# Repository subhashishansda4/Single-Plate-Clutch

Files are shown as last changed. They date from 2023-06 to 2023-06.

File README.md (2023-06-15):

## Description
Designed a Single Plate Clutch using mechanical calculations based on the below stated problem and data

**Single Plate Clutch transmitting 7kW power operated with electric motor running at 1400 rpm**

**Raw Data**
* Spline shaft material:-C15Mn75 IS 6967 Steel
* Yield shear strength for IS 6967 Steel =190N/mm2
* Factor of safety for spline shaft=3.0
* Stress concentration factor for spline shaft=2.0
* Rivet material:-Low carbon steel
* Shear stress for rivet material:-42 N/mm2
* No of rivets:-4
* Intensity of pressure for friction lining:- 0.06N/mm2
* Coefficient of friction for friction lining:- 0.15
* Spring Material:- Spring Steel(Stainless Steel)
* Spring Index:-6
* Allowable shear stress for the spring wire:-437.5 N/mm2
* Deflection of spring limited to 6.03 mm
* Modulus of rigidity for spring:-84 x 103 N/mm2
* Angle of pressure plate support:-450
* Bearing type:-Deep groove ball bearing
* Bearing size:-SKF(60 series)
* Bolt material for driving shaft flange:-M.S
* Allowable shear strength for bolt of driving shaft flange=40N/mm2
* Stud & Nut for spring attachment material:-Mild Steel
* Bush material: Brass
* Clutch plate material: Steel
* Pressure plate material: Steel
* Sleeve assembly material: Steel
* Flywheel material: Steel
* Driving shaft material: Steel

### Calculation
The full calculation report can be found here:\
[Calculation Report](https://github.com/subhashishansda4/Single-Plate-Clutch/blob/main/Design%20of%20Single%20Plate%20Clutch.pdf)

## Renders
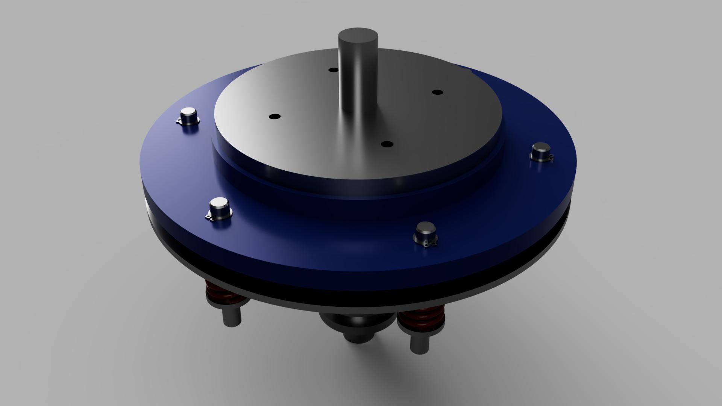
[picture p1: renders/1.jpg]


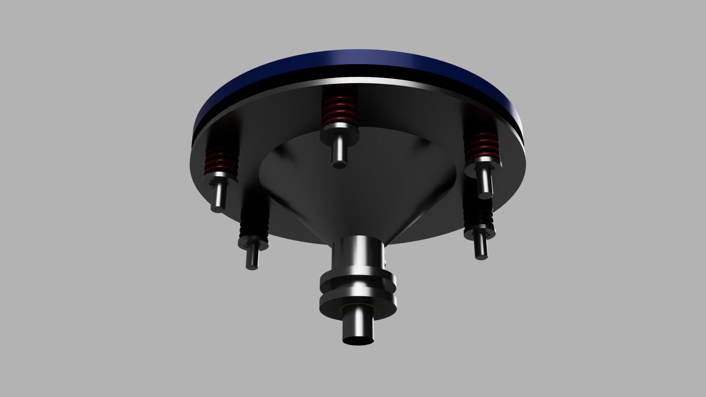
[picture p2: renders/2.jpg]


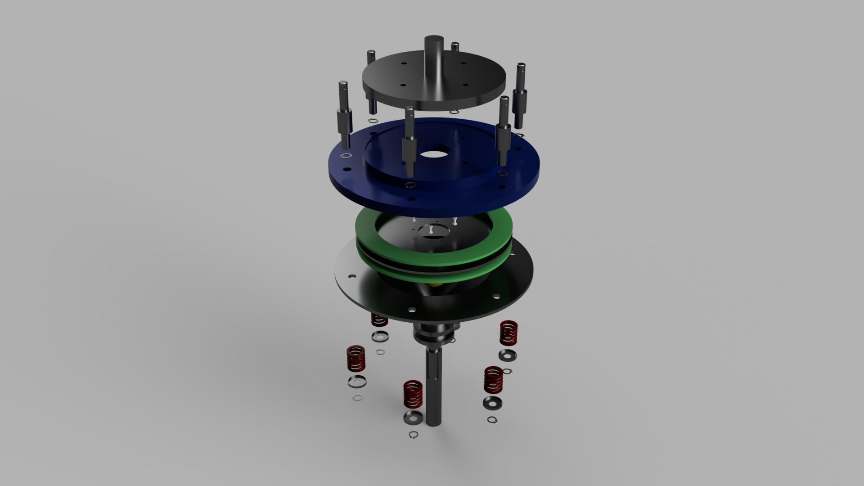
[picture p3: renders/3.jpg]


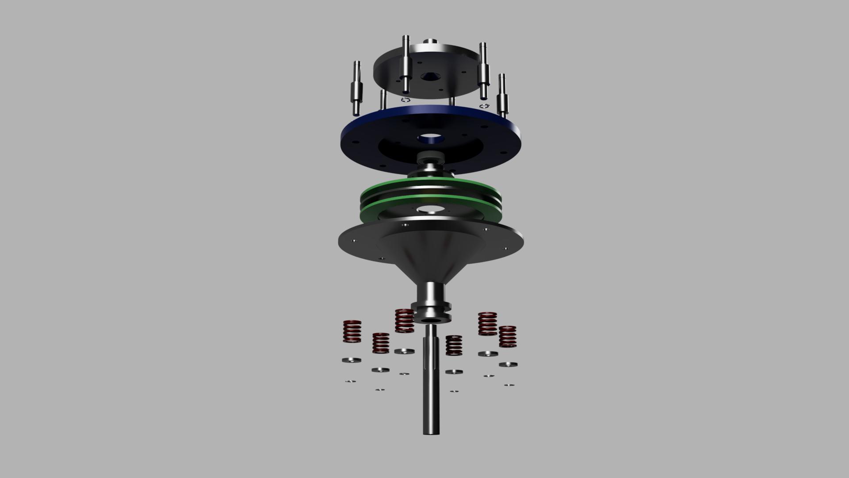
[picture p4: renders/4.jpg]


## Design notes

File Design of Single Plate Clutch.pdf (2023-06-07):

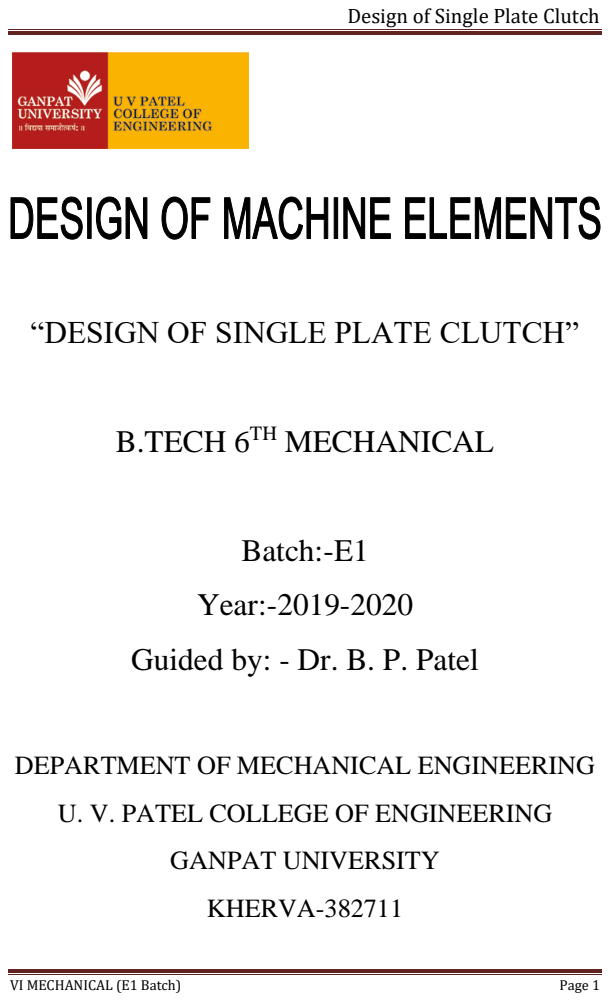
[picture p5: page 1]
VI MECHANICAL (E1 Batch); Page 1; B.TECH 6TH MECHANICAL; GANPAT UNIVERSITY; KHERVA-382711

Design of Single Plate Clutch

“DESIGN OF SINGLE PLATE CLUTCH”

Batch:-E1
Year:-2019-2020
Guided by: - Dr. B. P. Patel

DEPARTMENT OF MECHANICAL ENGINEERING

U. V. PATEL COLLEGE OF ENGINEERING

## CERTIFICATE

### This is to certify that Subhashis Hansda of roll no

17012031044 of 6

### th Mechanical Engineering has

### satisfactorily completed the course work in “Design of Single Plate Clutch” within four walls of U.V. Patel

College of Engineering, Kherva in the year of 2020.

Date of Submission: | Staff In charge

### Head of Department:

### U.V. Patel College of Engineering

### Ganpat University

### Kherva-382711

Design a single plate clutch which transmits 7kW power operated with electric motor running at 1400rpm. Use following data for single plate clutch. Assume the data is required.

- Spline shaft material:-C15Mn75 IS 6967 Steel
- Yield shear strength for IS 6967 Steel =190N/mm²
- Factor of safety for spline shaft=3.0
- Stress concentration factor for spline shaft=2.0
- Rivet material:-Low carbon steel
- Shear stress for rivet material:-42 N/mm²
- No of rivets:-4
- Intensity of pressure for friction lining:- 0.06N/mm²
- Coefficient of friction for friction lining:- 0.15
- Spring Material:- Spring Steel(Stainless Steel)
- Spring Index:-6
- Allowable shear stress for the spring wire:-437.5 N/mm²
- Deflection of spring limited to 6.03 mm
- Modulus of rigidity for spring:-84 x 10³ N/mm²
- Angle of pressure plate support:-45⁰
- Bearing type:-Deep groove ball bearing
- Bearing size:-SKF(60 series)
- Bolt material for driving shaft flange:-M.S
- Allowable shear strength for bolt of driving shaft flange=40N/mm²
- Stud & Nut for spring attachment material:-Mild Steel
- Bush material: Brass
- Clutch plate material: Steel
- Pressure plate material: Steel
- Sleeve assembly material: Steel
- Flywheel material: Steel

- Driving shaft material: Steel

NOTATIONS:-

SPLINE SHAFT

- P=Power to be transmitted=7kW
- N=Speed of the driving& driven shaft=1400rpm
- Ty=Yield shear strength for
- FOS=Factor of safety
- Kts=Stress concentration factor
- n=no of splines
- k=Type of fit
- d=Minor diameter of the spline shaft
- D=Major diameter of the spline shaft
- Ta=Allowable shear strength for spline shaft
- T=Average torque transmitted
- b= width of spline
- h=height of spline
- l=length of spline
- F=Shear force in spline shaft
- Dssb=dia of spline shaft for bearing seating
- Ls=total length of spline shaft

HUB FOR SPLINE SHAFT

- dho=Outer dia of hub , mm
- bh=Width of hub ,mm
- dhf=diameter of hub flange , mm
- LH= length of hub, mm
- Fahf=Axial force for hub flange , N

- thf=thickness of hub flange, mm
- PCDfr=Pitch circle diameter of flange rivet , mm

HUB FLANGE RIVET

- Tfr=Shear stress for hub material , N/mm²
- nr=no of rivets
- Fhfr=shear force for hub flange rivet ,mm
- dfrh=Head diameter of flange rivet, mm
- tfrh=Thickness of head flange rivet, mm
- lr=Standard length of rivet, mm

FRICTION LINING

- rmfl=Mean radius of friction lining
- bfl=Face width of friction lining
- Aff=Area of friction faces
- Wa=Axial force acting on the friction faces
- Pl=Intensity of pressure
- µ=Coefficient of friction
- nfs=no of friction surfaces
- tfl=Thickness of friction liner

CLUTCH PLATE

- r1=Outer radius of clutch plate
- r2=Inner radius of clutch plate
- rmfl=mean radius of clutch plate
- d1=Outer dia of clutch plate
- d2=Inner dia of clutch plate

- tcp=Thickness of clutch plate

SPRING

- Dm=Mean dia. of spring
- dsw=Dia. of spring wire
- Wtas=Total load on spring
- ns=No of springs required for axial load
- Ws=Max. Load on spring
- K=Wahl’s stress factor
- C=spring index
- Ts=Allowable shear stress for the spring wire
- na=No of active turns to the spring
- G=Modulus of rigidity
- Δ=Deflection/Compression of spring
- nf=Total No. of turns
- Lf=free length of spring
- psc=pitch of spring coil
- dis=Inside dia. of spring

BRASS-BUSH

- LB=length of bush
- D=Outer dia. of spline shaft
- Db=Outer dia. of brass bush

STUD & NUT

- lst=length of stud

- Dst=dia. of stud
- Pst=Pitch of stud ,mm

PRESSURE PLATE

- tpp=Thickness of pressure plate
- dopp=Outer dia. of pressure plate

ENGAGEMENT AND DISENGAGEMENT SLEEVE

- tes=Thickness of engagement sleeve
- tds=Thickness of disengagement sleeve
- bls=width of lever slot
- does=Outer dia. of engagement sleeve
- dds=Inner dia. of disengagement sleeve
- dis=Inner dia. of sleeve

FLYWHEEL

- tf=Thickness of flywheel
- dof=Outer dia. of flywheel
- dinf=Intermediate dia. of flywheel
- dif=Inner dia. of flywheel
- tfb=Thickness of flywheel near bearing
- tgf=groove depth inside flywheel

DRIVING SHAFT FLANGE

- Dds=driving shaft dia.(Dds=D)
- tdsf=Thickness of driving shaft flange
- dgsdf=dia. of groove inside driving shaft
- tgsdf=linear depth of groove inside driving shaft flange
- θc=Angle of cone inside driving shaft flange

BOLTS FOR DRIVING SHAFT FLANGE

- nb=No of bolts required
- db=dia. of bolt
- dPCDb=pitch circle dia. of bolt
- Tmax=max torque transmitted
- Tb=Allowable shear strength for bolt

NUT FOR BOLT OF DRIVING SHAFT FLANGE

- dn=dia of nut

BEARING

- dob=Outer dia. of bearing
- D*=Diameter( Reference)
- B=width of bearing
- r

*=radius(reference)

- r1

*=radius(reference)

(1) DESIGN OF SPLINE SHAFT AND HUB

Power P=7kW=7000W

Speed N=1400rpm

Spline Shaft Material =C15Mn75 (IS 6967) Steel

Yield Shear Strength of IS 6967, τy=190N/mm²

Assuming Factor of Safety =3.0 and

Approximate value of stress concentration factor =2

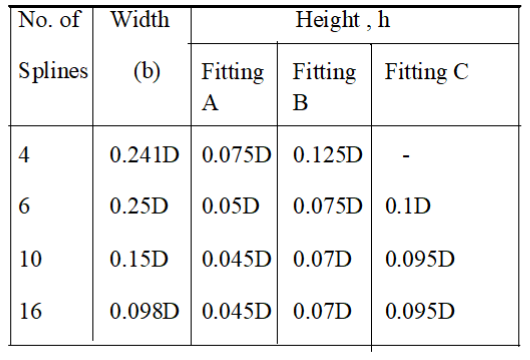
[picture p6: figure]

According to BIS splines are specified by four characters

nk x d x D (IS: 2327-1963)

Where

n=no of splines

k=type of fit

=A for permanent fit, P=21 N/mm²

=B for hub which is to slide when not under load P=14N/mm²

=C for hub which is to slide when not under load P=7N/mm²

Let

d is minor diameter of the spline shaft

D is major diameter of the spline shaft

The allowable shear strength Ta =

τy
FOS∗Kts

=

190
3∗2

= 31.667N/mm²

Average torque transmitted T=

60P
2πN

=

60∗7∗10³

2π1400

= 47.770Nm

Let us assume a shaft having 6 splines with class C fitting (where the hub can slide under the load). The permissible bearing pressure is 7N/mm²
.The standard proportions of splines are

Width b=0.25D

Height h=0.1D

The torque transmitting capacity of the hub is given by following relation

T =

1
2

pℎln(D − ℎ)

Where n=no of splines

And assuming length of hub l=1.5D

So 47.770 ∗ 10³ =

1
2

∗ 7 ∗ 0.1D ∗ 1.5D ∗ 6 ∗ (D − 0.1D)

D=25.62 mm

Standard Major Diameter of shaft,

Now | D=28mm | (As per design data book)

Minor diameter of shaft

d= (D-2

| D
| 10 )=28-2x²⁸
10

=22.4mm

Standard Minor diameter of shaft

d=23mm | (As per design data book)
Height, h=0.1D=0.1x28 | h=2.8mm

Width of spline (key) b=

D
4

=

28
4

= 7mm

b=6mm | (As per design data book)

Length of spline L=1.5D

=1.5*28=42mm

Now checking for the shear failure of the shaft

T =

π
16

d

3τy=16 ∗ 47.77 ∗

10³
π∗23³

= 20.00

N
mm²

Here,

- The value of the induced shear stress is less than the allowable shear Strength; hence the shaft is safe in shear.
- Now, Shear stress in Splines:-
- Shear force,

### 20.00 N/mm2

< 31.667N/mm2

F =²T
d
= 2 ∗ 47.770 ∗

10³

23
=4153.91 N

Induced Shear stress in Splines, τ =

F
bln

=

4153.91
6∗42∗6
= 2.747N/mm2
Here,

Which is also within the allowable limit.Hence, the design is safe.

- Design specification of the spline: 6C x 23 x 28
- Outer diameter of hub(dho) =1.75D
=1.75*28=49 mm
- Width of hub (bh)= 1.25D =1.25x28
=35 mm
- Diameter of hub flange (dhf)=3D =3x28 =84mm
- Axial force for hub flange Fdhf =2dho*P*(

dℎf−dℎo
2

)

### 2.747 N/mm2

<31.6N/mm2

=2*49*7*⁸⁴⁻⁴⁹
2
=12005 N
- Pitch circle diameter of flange Pcdfr= (

dℎf−dℎo
2

) + dho

=

84−49
2

+ 49

Pcdfr =66.5 mm

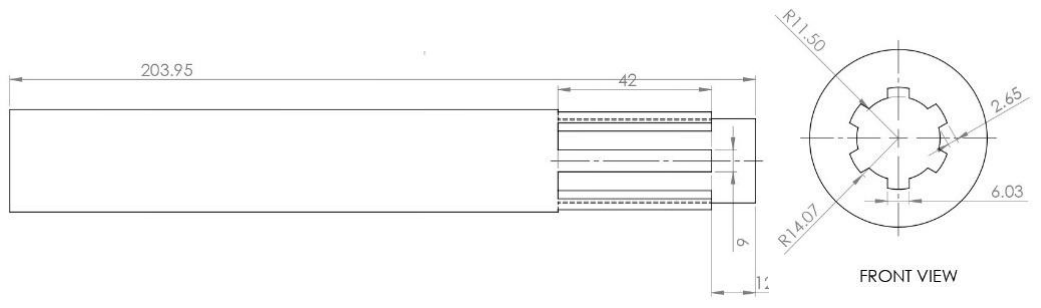
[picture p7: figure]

(2) RIVET
- Material: Low Carbon Steel
- Shear stress τth =42 N/mm²
- No of rivets = 4
- Shear force for hub flange rivet

Fhfr=

2T

PCDfr

=

2∗47.77∗1000
66.5
=1436.69 N
- Also , shear force for hub flange rivet Fhfr=nf x

π
4

x dfr2 x τfr

1436.69 = 4 x (3.14/4) x dfr2 x 42 dfr=3.30 mm

dfr~4 mm

- Head diameter of flange rivet dhfr=2 x dfr = 2 x 4
= 8 mm
- Thickness of head of flange of rivet thfr=

dfr
2

=

4
2

= 2 mm

- Standard length of rivet =20 mm

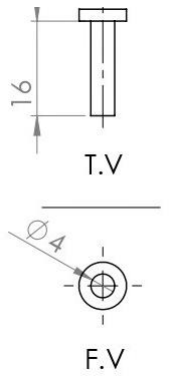
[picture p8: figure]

(3) Mean radius and face width of the friction lining

Let,rmfl = Mean radius of the friction lining
bfl = Face width of the friction lining

=

rmfl

4
- We know that the area of the friction faces,
Aff = 2 πrmfl ∙ bfl
- Normal or the axial force acting on the friction lining.
Wa = Aff × Pi
= 2 πrmfl ∙ bfl ∙ Pi

And torque transmitted,
T = μWarmfl ∙ nfs
= μ (2 rmfl ∙ bfl ∙ Pi

)rmfl ∙ nfs

Here, bfl =

rmfl

4

, nfs = no. of friction lining = 2

- The intensity of pressure (Pi

) as 0.06N/mm²
and Co-efficient of
friction (μ) as 0.15, we have

∴ 47.77 ∗ 10³
∗ 2 = 3.14 ∗ 0.15 ∗ rmf1

3
∗ 0.06 ∗ 2

rmf1 = 118.55 mm

= 120 mm(approx)

And, bfl =

rmfl

4

=

120
4

bfl = 30 mm

rmfl ≅ 120mm

T =

π
2
- μ ∙ rmfl

3
- Pi
- nfs

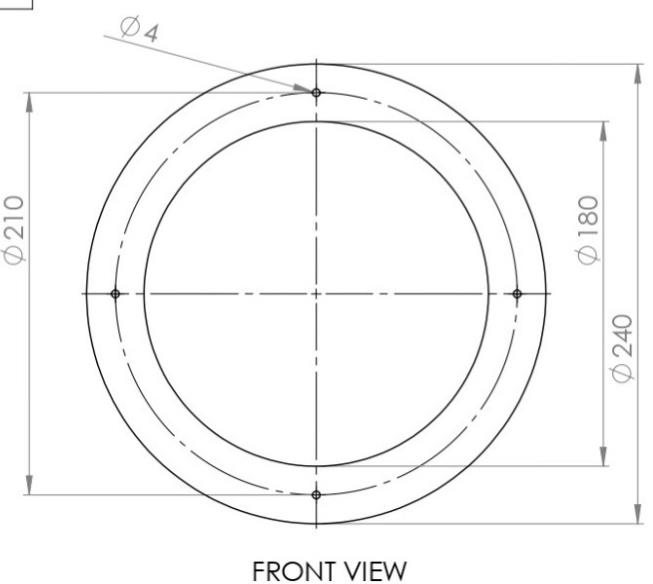
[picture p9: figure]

(4) Outer and Inner radii of clutch Plate

Let,
r1andr2 = Outer and inner radii of the clutch plate respectively.
- Since the face width (or radial width) of the plate is equal to the difference of the Outer and inner radii, therefore
bfl = r1 - r2
OR
r1 - r2 = 30 | (1)
- We know that for uniform Wear, mean radius of the clutch plate,

rmfl =

r1+ r2
2
OR
r1 + r2 = 2 rmfl
= 2 × 120
r1 + r2 = 240 | (2)
- By solving eqn
(1) and (2) we get,

r1 = 140 mm | d1 = 280 mm
r2 = 105 mm | d2 = 210 mm

(Table-2.Preferred dimensions for clutch facings for an automotive transmission.)

- Standardize the Outer and inner dia. Of the clutch plate. (Ref. Table (2))
- Thickness of the clutch plate (Ref. Table(2))
tcp = 3 mm
- Thickness of friction lines,

tfl = 1.2 tcp
= 1.2×3
= 3.6mm

tfl=3.6mm

Preferred outside diameter (mm): 120,125,130,135,140,145,150,155,160,170,180,190, 200,210,220,230,240,250,260,270,280,290,300,325 and
350
Preferred inside diameter (mm): 80,85,90,95,100,105,110,120,130,140,150,175, and 200
Preferred thickness (mm): 3, 3.5 and 4
Rivet holding land: Net less than 1.45 mm and greater than half the thickness of facing.
r1 = 142.5 mm | d1 = 285mm | r2 = 100 mm | d2 = 200 mm

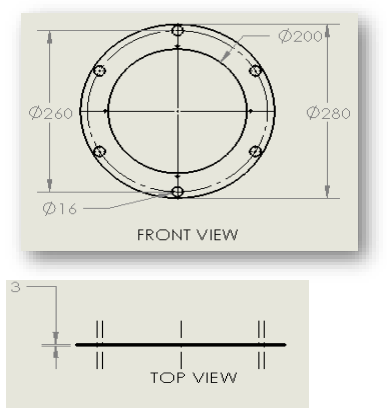
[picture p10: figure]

(5) Dimensions of Spring

Let, Dm = Mean diameter of the spring.
dsw = Diameter of the spring Wire.
- Spring material : Spring Steel(Stainless Steel)
- We know that the axial force on the friction faces,

Wa = 2 πrmfl ∙ bfl ∙ Pi
= 2π*120*30*0.06
Wa = 1356.48 N

In Order to allow for adjustment and for maximum engine torque the spring is designed for an overload of 30%.

∴ Total load on the springs,
Wtas = 1.3Wa
= 1.3×1356.48
= 1763.424 N

Wtas ≅1770 N

- No. of spring req. for given axial load, ns = 0.04D + 5
= 0.04× 28 + 5
= 6.12
- Since there are 6 Spring, therefore Max. load on each spring, Ws =

Wtas
ns

=

1770
6
- We know that Wahl’s Stress factor,

k = 4c−1
4c−4

+

0.615
c

where c = spring index = 6 (given)

k = 4×6−1
4×6−4

+

0.615
6

k = 1.2525

- We also know that maximum Shear Stress induced in the wire. (τs
).

ns ≅ 6

Ws =295 N

Let,τs = allowable shear stress for the spring wire τs =437.5N/mm²

τs

= k ×

8Wsc
π×(dsw)

2

∴ 437.5 = (1.2525 ∗ 8 ∗ 295 ∗ 6)/(π ∗ dsw

2
)

We shall take a standard wire of size SWG9 diameter

∴ dsw ≅ 3. 658mm

And mean diameter of the spring.
Dm = C∙ dsw
= 6 ×3.658
= 21.948mm
Dm= 22 mm
- Deflection of spring is limited to 6.03 mm. (given)

∴ Let, na = no. of active turns of the spring.
G = 84× 10³N/mm²
(given)

∴Deflection of the spring or compression of the spring, δ =

8Wsc

3na

G∙dsw

∴ 6.03 =

(8 ∗ 295 ∗ 6

3
∗ na

)
84 ∗ 10³ ∗ 3.658
= 3.634

na≅ 4

- No. of active turn of spring

dsw = 3.5930 mm

- Assuming squared and ground ends, Total No. of turns, nt = na + 2 nt = 4 + 2nt= 6
- Free length of the spring,
Lf = nt
- dsw + δ + 0.15 δ
= (6×3.658) + 6.03+(0.15×6.03)
- Pitch of the spring coils,

psc =

Lf
nt−1

=

28.88
5

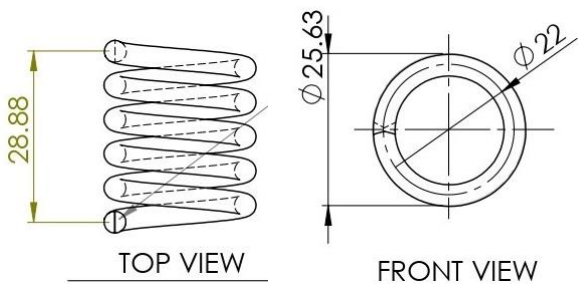
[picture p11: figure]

(6) Brass-Bush for spline shaft

Let, lb = length of bush

na ≅ 4

Lf = 28.88mm ≅ 28.88mm

psc = 5.776 mm≅ 5.776mm

D = Outer diameter of spline shaft.

- Outer diameter of brass bush, db =1.25 D = 1.25 ×28
db =35 mm
- Length of brass- bush
lb = 2.25 D = 2.25×28
lb = 63 mm

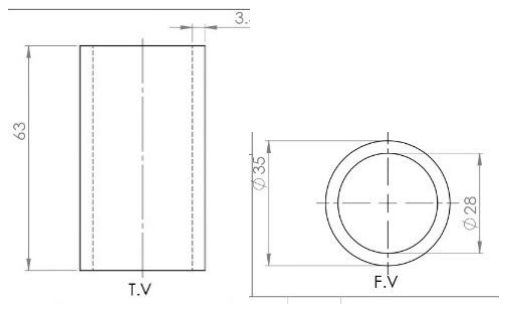
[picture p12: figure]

(7) Stud & Nut

Stud & Nut material :- Mild Steel (M.S)

Inside diameter of spring dis=Dm – dsw
=22-3.658 =18.342 mm

Based on inside diameter of spring, selected size of stud is

M16 x 10 mm

Calculated length of stud= 95 mm

Selected length of stud = 96 mm

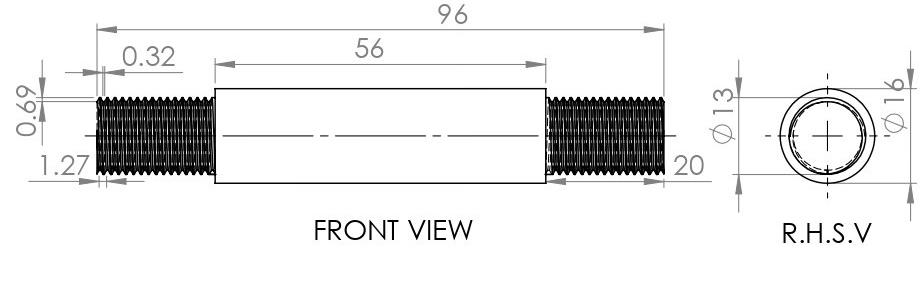
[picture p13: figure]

(8) Pressure Plate
- Angle of pressure plate support with horizontal = 45°
- Thickness of pressure plate,
tpp = 1.5 × tcp
= 1.5 ×3
tpp = 4.5 mm
- Outer dia. Of pressure plate (dopp ):-

dopp

= 1.15 d1
= 1.15 ×270

∴ dopp
= 310.5 mm

dopp

≅230 mm

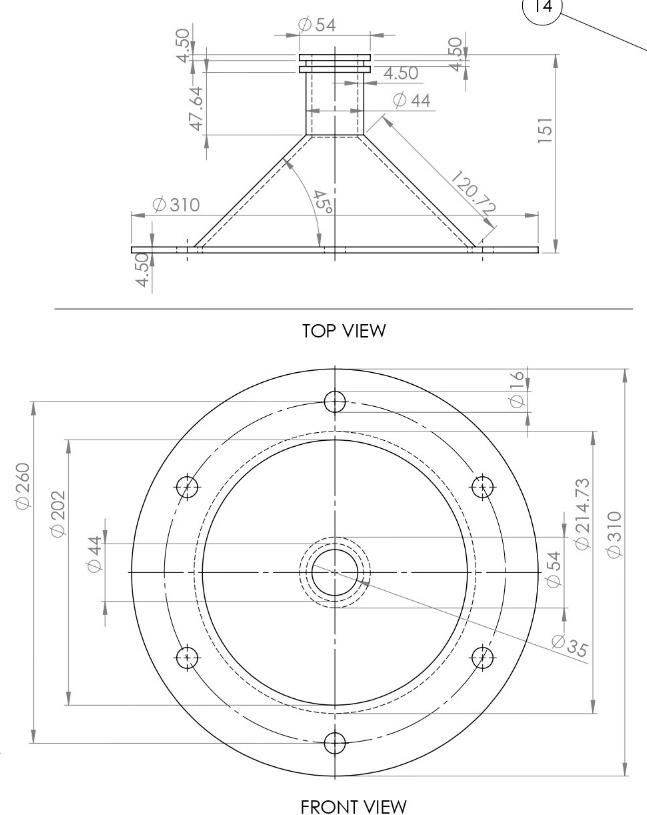
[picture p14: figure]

(9) Engagement & Disengagement Sleeve
- Thickness of Engagement sleeve,
tes = 1.5 tpp
= 1.5 ×4.5
- Thickness of disengagement sleeve,
- Width of lever slot,
bls = 2tpp = 2×4.5
- Outer dia. Of engagement sleeve,

does
= 2.5D
= 2.5 ×28

tds= tes = 6.75 mm

bls = 9 mm

does
= 70 mm

tes = 6.75 mm

- Outer dia. Of disengagement sleeve,
- Inner dia. Of sleeve,
dis= 1.75D
= 1.75 ×28
(10) Flywheel
- Thickness of flywheel.
tf = 0.5D
= 0.5 × 28
- Outer dia. Of flywheel,
dof = 1.15 d1
= 1.15 ×270
= 310.5 mm
- Intermediate dia. Of flywheel, dinf = 0.75 d1
= 0.75 ×270
- Inner dia. Of flywheel(∴based on bearing outer dia.dob = dif
= 42 mm)

does

= dds = 70 mm

dis = 49 mm

tf = 14 mm

dof ≅310 mm

dinf= 202.5 mm

dinf= 42 mm

- Thickness of flywheel near bearing,

where, B = bearing width

Bearing No: SKF 6004 (Given)
(Ref. DDB Pg. no. 4.12)
- Groove depth inside flywheel approximate,

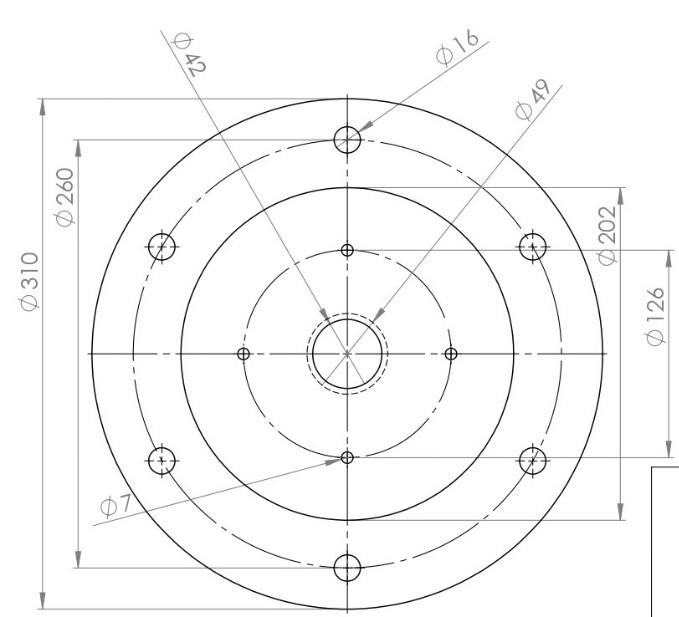
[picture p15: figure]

(11) Driving Shaft Flange

Now,

- Driving shaft dia.

tfb = B = 14 mm

tgf =0.5 mm

Dds= D = 28 mm

- Thickness of driving shaft flange,
- Outer dia. Of driving shaft flange ,

Dods = 7.5 Dds
= 7.5×28
- Dia. Of groove inside during shaft flange:

dgdsf = 1.25 Dds
= 1.25×28
- Linear depth of groove inside driving shaft flange, tgdsf = 3 mm (Approx.)
- Angle of cone inside driving shaft flange,

tdsf=tf = 14 mm

Dods= 210 mm

dgdsf= 35 mm

θs = 45°

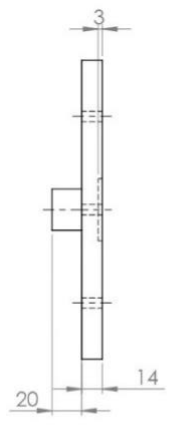
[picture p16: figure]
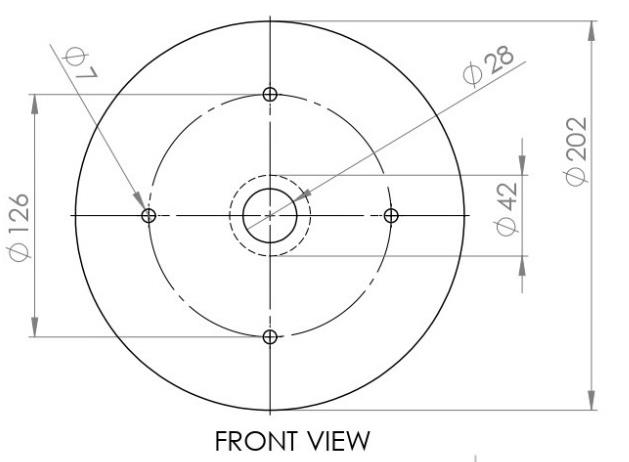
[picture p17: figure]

(12) Bolts for driving shaft flange
- No. of bolts required,

nb =

Dds
50

+ 3

=

38
50

+ 3
= 3.56
- Dia. Of bolt,

db=

0.5 Dds
√nb
=

0.5∗28
2
= 7 mm

(std. dia. Of bolt)

- Pitch circle dia. Of bolt,

dPCDb

= 4.5 Dds

= 4.5 ×28

- We know that average torque transmitted,

T = 47.77 x10³N.mm

nb= 4

db = 8 mm

dPCDb
= 126 mm

∴For safer design the max. torque transmitted is 25% more than average torque transmitted,

Tmax = 1.25×T = 1.25 ×47.77 x10³
Tmax = 59.68 x10³N. mm
- Material of bolt : M.S (Given)
- The allowable shear strength for bolt is 40 N/mm²

∴ τball= 40 N/mm²

- Checking of bolt for shear stress.

∴ Tmax = nb ×

π
4

× db

2
- τb ∙

dPCDb
2

59.68 ∗ 10³ = 4 ∗

π
4

∗ 8

2
∗ τb ∗

126
2

∴ τb = 2.70 N/mm²

- τb = 2.70N/mm²<τball = 40 N/mm² ∴The design is safe for bolt in shear.

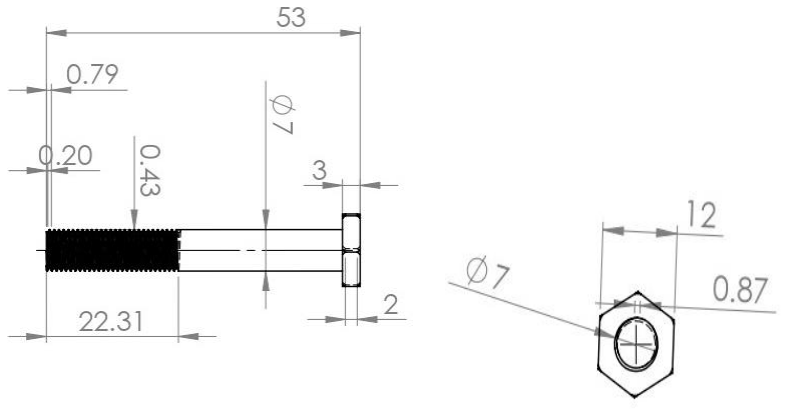
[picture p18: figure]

(`13) Nut for bolt of Driving Shaft Flange

Selected nut : M16

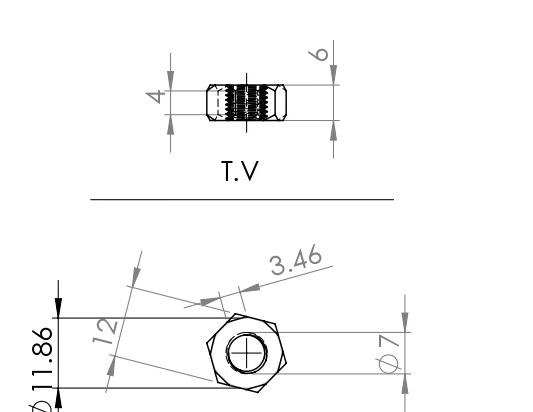
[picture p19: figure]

### 14 Bearing

- Selected bearing: SKF 6004 (From DDB1: - Deep groove ball bearing)
- Diameter of spline shaft, D = 28 mm
- Diameter of spline shaft for bearing seating, Dssb = 23 mm
- Outer dia. Of bearing dob = 42 mm
- Diameter, D

∗ = 36 mm
- Width of bearing, B = 12 mm
- Radius, r

∗ = 1 mm
- Radius, r1

∗ = 0.6 mm
- Total length of spline shaft L=150 mm
- Deep groove ball bearing is selected because there are max no of ball fitted in the race. Therefore, the load carrying capacity and running speed is increase.
- The load carrying capacity is depend on ball size and no of ball
- SKF is a group of US bearing maker.

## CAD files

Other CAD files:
clutch assembly v11/01 DRIVING SHAFT FLANGE.ipt
clutch assembly v11/02 FLYWHEEL.ipt
clutch assembly v11/03 SPLINE SHAFT.ipt
clutch assembly v11/04 SPLINE HUB.ipt
clutch assembly v11/05 PRESSURE PLATE.ipt
clutch assembly v11/06CLUTCH PLATE.ipt
clutch assembly v11/07 BUSH.ipt
clutch assembly v11/08 STUD.ipt
clutch assembly v11/09 SPRING.ipt
clutch assembly v11/10 WASHER.ipt
clutch assembly v11/11 CIRCLIP.ipt
clutch assembly v11/14 RING.ipt
clutch assembly v11/15 NEW RIVET.ipt
clutch assembly v11/16 BEARING.iam
clutch assembly v11/CLUTCH ASSEMBLY.iam
clutch assembly v11/_6005_RSL_PART1_2.ipt
clutch assembly v11/_6005_RSL_PART2_4.ipt
clutch assembly v11/_6005_RSL_PART3_6.ipt
